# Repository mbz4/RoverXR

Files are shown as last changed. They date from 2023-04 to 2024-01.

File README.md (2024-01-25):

# RoverXR

OSHW EE000002

https://certification.oshwa.org/ee000002.html

## Open Source Teleop Demo For Students

Teleoperation { Low-Latency Video + Virtual Scene + M5 Rover C Pro} Fun

# Repository tree

```bash
📦RoverXR (edu_teleop_demo)
 ┣ 📂Blueprints
 ┃ ┣ 📂CAD
 ┃ ┣ 📂Figures
 ┃ ┣ 📂Firmware
 ┃ ┣ 📂Godot
 ┃ ┣ 📂Install
 ┃ ┣ 📂Testing
 ┃ ┣ 📜stream_mjpeg_ws.py
 ┃ ┗ 📜README.md
 ┣ 📂Thesisaurus
 ┃ ┣ 📂Future
 ┃ ┣ 📂Poster
 ┃ ┣ 📂Stream Testing
 ┃ ┣ 📂Survey
 ┃ ┣ 📂Workload Analysis
 ┃ ┣ 📜README.md
 ┃ ┗ 📜Zorec_XR_teleop_demo_dev_MSC.pdf
 ┣ 📜LICENSE
 ┗ 📜README.md
```

### BibTex

```
@misc{Zorec_2023, 
    title={XR TELEOPERATION DEMO DEVELOPMENT}, 
    url={https://github.com/mbz4/RoverXR}, 
    publisher={University of Tartu}, 
    author={Zorec, Matevž Borjan}, 
    year={2023}, 
    month={May},
    keywords = {teleoperation,godot-engine,video-streaming,augmented-reality,educational}
    }
```

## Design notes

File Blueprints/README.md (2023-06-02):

# Blueprints

## CAD, ELE, FW, HOW-TO

### Blueprints Tree

```
📦Blueprints
 ┣ 📂CAD
 ┣ 📂Figures
 ┣ 📂Firmware
 ┣ 📂Godot
 ┣ 📂Install
 ┣ 📂Testing
 ┣ 📜stream_mjpeg_ws.py
 ┗ 📜README.md
```

## Link to Pi2AR apk

[Pi2AR apk](https://drive.google.com/file/d/1Cv3eQTNefOODzdWp3nt191eAGhhzpHHq/view?usp=sharing)

## Link to 2D Demo scene

[2D demo executable](https://drive.google.com/file/d/1SQd6SBSPiZBGjC4s-J33E9EYQUEvNkwV/view?usp=sharing)

# Pi-Side Setup

0. flash Raspbian Lite (32-bit) onto SD Card (class 10 recommended), then run

    `sudo apt-get update && sudo apt-get upgrade -y`

    - expand filesystem, adjust settings, hostname, enable SSH etc
    
    `sudo raspi-config`
    
    - adjust network settings: Wifi, etc

1. get the repo to the pi

    `git clone https://github.com/mbz4/edu_teleop_demo.git`

2. to start streaming, running the following python script 

    `Blueprints/stream_mjpeg_ws.py`

    - it configures the camera using picamera2
    - prepares a byte buffer in memory
    - starts a websocket server at:

        `ws://<PI-IP>:3333`
    
    - once a client connects
        
        - it sends individual JPEG frames from picamera2 output buffer

# VR setup

1. get scene apk to your Meta Quest 2

    - once loaded you can use controller thumbsticks to rotate, navigate the AR scene
        - behind you is a terminal window
        - you can set the websocket URI address here - input just the Pi IP:

        `PI_IP > PI_IP_ADDRESS_IN_YOUR_LOCAL_NETWORK`

        - (make sure you are connected to the same network as the pi is)
    - disable space sense
    
2. run apk

# M5 Rover C setup

1. print mod kit file 

    - gcode (sliced for Prusa MK3S) found at:

    `Blueprints/CAD/32g_rover_mod_kit_0.3mm_PLA_MK3S_2h12m.gcode` 

    - v1 3mf model files found at:

    `Blueprints/CAD/rover_mod_kit.3mf`

2. assemble the mod kit
 
#### [Bill of materials for physical artefact](./CAD/README.md)

#### Fusion360 RoverXR assembly link [f360 assembly link](https://a360.co/4158f0r)

Please, note the above link may not function correctly if viewed on mobile.

#### v2 concept design for reference

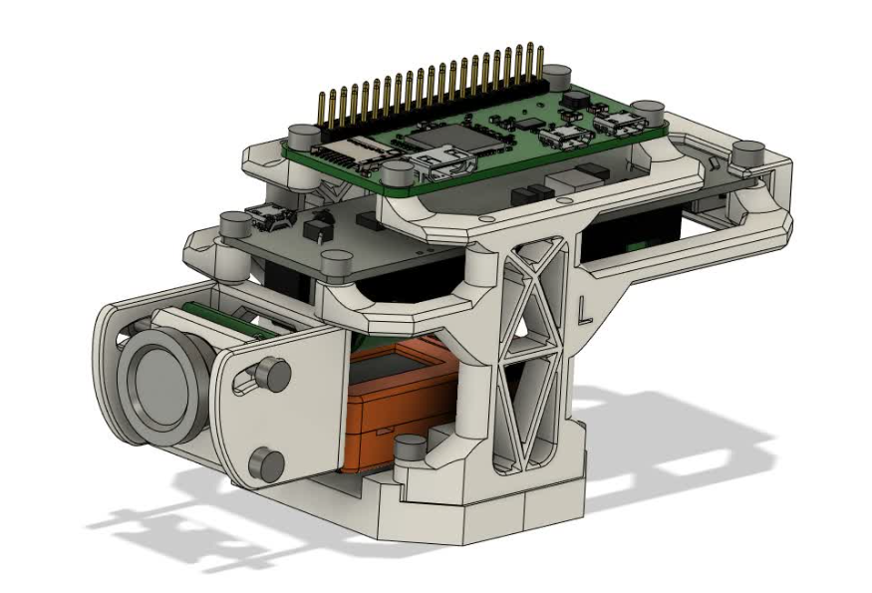
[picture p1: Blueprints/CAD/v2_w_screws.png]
Assembled v2 with screws


3. flash firmware, can use Arduino IDE (M5 Stick C library)

    - connect rover M5 Stick C to PC
    - open & flash master scripts, found at:

    `Blueprints/rover_FW/Master/Master.ino`

    - disconnect from PC and install Master Stick to Rover
    - connect remote M5 Stick C to PC
    - open & flash remote controller script, found at:

    `Blueprints/rover_FW/Remote/Remote.ino`

    - disconnect from PC and install Remote Stick to Remote Controller
    - use power switches on remote & rover
    - press and hold for 4 seconds the lower left side button on both M5 Stick C's to turn them on
    - press and hold for 4 seconds the 'M5' button on Remote controller, once the Master MAC address is shown
    - rover can now be remotely operated using remote

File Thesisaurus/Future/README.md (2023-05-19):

# Future Work Recommendations

graphic

|Title |Key points |Description |
|---|---|---|
|RoverXR  Hardware  Modifications|Integrate Pi Zero 2 W |Possible to bypass and omit M5 Stick C on the Rover and Remote. Zero 2 W could directly convey driving commands from VR  using a second websocket stream. The M5 Rovers battery can power the Zero 2 W directly. Improved multithreading enables more complex teleoperation solutions. |
| |New enclosed snap-fit shell|Design fully enclosed, transparent, compliant snap-fit shell for easy access  and a more seamless aesthetic.  Making it flexible and rounded should improve feel when handling. |
| |New camera |Install wide field of view camera with motorised focusing. |
| |Adjustable camera angle |Add servo for adjusting camera angle on the fly. Additionally, modify current camera mount to  accommodate additional 15 degrees to the downward facing angle. |
| |Add shutdown button |Expand breakout board with shutdown button for triggering poweroff command. |
| |Improve interface |Add more status indicators to better inform a user of status of the device  without having to SSH in.  This could include various assortment of LEDs or a small OLED. |
| |Develop a charging base |Currently the setup consists of two devices, easy to misplace. With a dedicated charging base/enclosure,  they would have a place to rest & recharge.  This would in turn help to reduce the risk of misplacement. |
| |Add sensors |Usually teleoperated robots are equipped with various sensors,  enabling extero- and proprioception. This could be used to complement  a new VR interface solution, which better informs the operator of both the status  of the vehicle as well as its surroundings. Three key sensory features to consider include: LiDAR, Microphone, battery voltage monitor. |
| |Remote controller mount |The current chassis could be extended by integrating  a simple remote controller mount. This may help reduce the chance of misplacing  either component as they are intended to work as a pair. |
|RoverXR Software Modifications  |Improve streaming solution |The video stream solution consists of two components: a RPi based server,  serving the video stream, and a Godot scene,  which connects to the server and displays the individual frames.  Investigating alternative protocols, encoding and rendering techniques  could improve the quality of the video stream. Remote streaming configuration should also be added, such as basic video quality settings etc. |
| |Godot |The overall scene can be expanded by adding more informative interfaces. |
| |Autonomous driving mode |With an upgraded RPi unit capable of controlling movement,  autonomous operation is easier to implement. |
| |Deploy ROS |This would allow for more complex teleoperation solutions, as well as provide topic based control and access to a wide variety of devices  with ready made drivers, making future development more cost effective. A Godot-ROS-Bridge could be implemented for a more seamless development experience. Ready made SLAM and autonomous driving solutions would also be available. However, this may require a further a more capable external compute component in the setup|
| |Control from VR |Implement RoverXR control interface in a Godot VR scene to control the movement. |
| |Godot H264 decoding |Explore ways for decoding video streams natively in Godot. One possible solution may be the 'ffmpeg-node' for Godot 3.x |
|RoverXR Evaluation Ideas |Unity solution |Prepare an equivalent interface using the Unity game engine to compare performance. |
| |Compare with FPV |Comparative study to commercial drone FPV setups,  like the DJI FPV Combo product series. An OpenHD and EZ-WiFiBroadcaster implementation should also be explored.  These represent some of the most comprehensive and best performing FPV solutions. |
| |Further evaluate solution  |Ideas to explore, such as evaluating interface intuitiveness/immersiveness,  setup complexity, task completion time etc |

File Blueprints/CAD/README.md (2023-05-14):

# CAD Tree

```
📦CAD
 ┣ 📂v1
 ┃ ┣ 📜32g_rover_mod_kit_0.3mm_PLA_MK3S_2h12m.gcode
 ┃ ┣ 📜rover_mod_kit.3mf
 ┃ ┗ 📜v1.png
 ┣ 📂v2
 ┃ ┣ 📂3mf
 ┃ ┃ ┣ 📂deprecated
 ┃ ┃ ┃ ┣ 📜assorted_camera_mounts.3mf
 ┃ ┃ ┃ ┣ 📜camera_mounting_shroud v15.3mf
 ┃ ┃ ┃ ┣ 📜camera_mounting_shroud v16.3mf
 ┃ ┃ ┃ ┣ 📜camera_mounting_shroud_3,04mm_focal_adjust v10.3mf
 ┃ ┃ ┃ ┣ 📜camera_mounting_shroud_3,04mm_focal_adjust v11.3mf
 ┃ ┃ ┃ ┗ 📜rear_port_bumber v32.3mf
 ┃ ┃ ┣ 📜adjustable_camera_shroud_mount_w_lens.3mf
 ┃ ┃ ┣ 📜bumper_maglock_adapter v23.3mf
 ┃ ┃ ┣ 📜bumper_maglock_adapter_cap v23.3mf
 ┃ ┃ ┣ 📜camera_mounting_shroud v21.3mf
 ┃ ┃ ┣ 📜joy_c_remote_adapter v22.3mf
 ┃ ┃ ┣ 📜joy_c_remote_adapter_cap v22.3mf
 ┃ ┃ ┣ 📜maglock_adapter_kit.3mf
 ┃ ┃ ┣ 📜mounting_adapter_v2 v66.3mf
 ┃ ┃ ┗ 📜rear_port_bumber v34.3mf
 ┃ ┣ 📂f3z
 ┃ ┃ ┗ 📜assembly v68.f3z
 ┃ ┣ 📂step
 ┃ ┃ ┣ 📜adjustable_camera_shroud_mount_w_lens.step
 ┃ ┃ ┣ 📜assembly v68.step
 ┃ ┃ ┣ 📜camera_mounting_shroud.step
 ┃ ┃ ┣ 📜mounting_adapter_v2 v66.step
 ┃ ┃ ┗ 📜rear_port_bumber v32.step
 ┃ ┣ 📜38g_full_mod_kit_v2_0.2mm_PLA_MK3S_4h47m.gcode
 ┃ ┣ 📜3g_maglock_adapter_kit_0.2mm_PLA_MK3S_29m.gcode
 ┃ ┣ 📜mod_kit_v2.3mf
 ┃ ┣ 📜v2.png
 ┃ ┗ 📜v2_w_screws.png
 ┣ 📜assembly v77.avi
 ┣ 📜README.md
 ┣ 📜v0_concept_phase.png
 ┣ 📜v1.png
 ┗ 📜v2_w_screws.png
```

# Bill of materials

|Component |Description |Features |QTY|Cost Per  [EUR]|Cost  [EUR]|
|---|---|---|---|---|---|
|M5 Rover C Pro |Programmable Mecanum wheel omnidirectional robot base. 4x N20 worm gear motors to drive the wheels directly by the motor driver. Servo gripping mechanism. |I2C Address 0x38, remote control, gripper Programmable, Four-channel motor driver, Extra Grove ports for expansion, STM32F030C6T6, I2C 16340(700mAh) battery holder|1  |60 |60 |
|Wemos Battery Shield |18650 Battery Shield (V3) for Raspberry Pi & Arduino Cheap, portable power supply module. |In: 5V/500mA (Micro USB) Out: 5VDC (USB type A) 3x 5VDC (up to 4A) + 3x 3VDC (up to 1A) Battery Charging /  Charged LEDs Overcharge, Deep Discharge Protection |1  |2.5 |2.5 |
|18650 Li-Ion |Battery: Samsung Li-Ion 18650 cell |3.6V 2600mAh |1  |11 |11 |
|M5StickC ESP32 |M5 Stick C is a mini M5 Stack, powered by ESP32.  It is a portable, easy-to-use, open source, IoT development board. |ESP32-based, IMU, LED, IR, Mic,  3 buttons, LCD(0.96 in), battery Wearable / Wall mounted, support: UIFlow, MicroPython, Arduino, .NET nanoFramework |2  |13.7 |27.4 |
|JoyC Omni-directional Controller|Rocker module for the M5 Stick C & Rover base. |STM32F030F4, I2C, 12 RGB LEDs omni-directional movement & button press  16340 battery holder |1  |18.2 |18.2 |
|Raspberry Pi Zero 1 W v1.3 |Flexible, compact Raspberry Pi Single Board Computer. Size: 65mm long by 30mm wide, affordable. |1GHz single-core CPU, 512MB RAM Mini HDMI port, Micro USB OTG port Micro USB power, HAT-compatible 40-pin header CSI camera connector WiFi (2.4GHz) & Bluetooth |1  |13.7 |13.7 |
|Raspberry Pi Camera Board v2.1  |High quality camera based on Sony IMX219PQ image sensor. Supports FHD video and still photographs. |Fixed focus lens, 8 megapixel resolution  Support 1080p30, 720p60, 480p90 25mm x 23mm x 9mm, just over 3g; CSI connector |1  |23.65 |23.65 |
|CSI Camera Ribbon Adapter |Raspberry Pi Zero adapter cable to Camera CSI connector |Length: 15 cm, CSI 22-pin (Pi Zero) to 15-pin (Camera board) |1  |5.12 |5.12 |
|0.67x Wide Angle, Macro, Fisheye|Magnetic interlocking lens camera add-on kit |Self-adhesive metal ring mount 0.67x wide angle, macro lens combo 180 deg field of view fisheye lens |1  |7 |7 |
|Totals |Listed Prices: April 2023 |Total Part Count: |10 |Total [EUR]: |168.57 |

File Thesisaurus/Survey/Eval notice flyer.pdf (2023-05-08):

### Ad hoc event notice:

## Thesis artefact evaluation

## From 15:00 Until 18:00

## Please, do not interrupt ongoing experiments

If you wish to partake or have concerns, please contact student responsible.

If you’d like to help me evaluate and experience a cool new teleop demo, please talk to me for a testing slot!

Student responsible: Matevž Zorec Contact: matevz.zorec@gmail.com

Tartu, May 9

th 2023

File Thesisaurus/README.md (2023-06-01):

# Thesisaurus Tree

## Defense presentation link

[XR TELEOP DEMO DEV](https://docs.google.com/presentation/d/17Uub06jR5xMtjwQKw79iaS7XjQxCx0AH1VZ0uDm-VvA/edit?usp=sharing)

```
 ┣ 📂Future
 ┃ ┗ 📜README.md
 ┣ 📂Poster
 ┃ ┗ 📜A0_mbz_XR_Demo_poster.pdf
 ┣ 📂Stream Testing
 ┃ ┗ 📜README.md
 ┣ 📂Survey
 ┃ ┣ 📂evaluation_event
 ┃ ┃ ┣ 📜20230509_155246.mp4
 ┃ ┃ ┣ 📜20230509_160718.mp4
 ┃ ┃ ┗ 📜blurred_out_survey_participant.jpg
 ┃ ┣ 📂word_clouds
 ┃ ┃ ┣ 📜how_do_you_feel_about_the_interface_in_the_setup.png
 ┃ ┃ ┣ 📜please_describe_the_rover.png
 ┃ ┃ ┣ 📜please_describe_your_experience_with_the_rover.png
 ┃ ┃ ┣ 📜please_share_your_thoughts_on_how_to_improve_the_setup.png
 ┃ ┃ ┣ 📜ROSETTA_how_do_you_feel_about_the_interface_in_the_setup.png
 ┃ ┃ ┣ 📜ROSETTA_please_describe_the_rover.png
 ┃ ┃ ┣ 📜ROSETTA_please_describe_your_experience_with_the_rover.png
 ┃ ┃ ┗ 📜ROSETTA_please__share_your_thoughts_on_how_to_improve_the_overall_setup.png
 ┃ ┣ 📜Eval notice flyer.pdf
 ┃ ┗ 📜README.md
 ┣ 📂Workload Analysis
 ┃ ┗ 📜README.md
 ┗ 📜README.md
```

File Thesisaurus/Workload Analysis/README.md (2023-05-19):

# Extended Thesis Workload Analysis

|Task |Description |Time  Invested  [hrs]|
|---|---|---|
|VR & background |- read:  “The VR Book: Human-Centered Design for Virtual Reality” by Jason Jerald - preliminary literature review - understanding teleoperation, motivation - isolating problem statement |25 |
|Reviewing previous works |- reviewing previous teleoperation thesis works - experience teleoperating & developing with Donkey Car S1 - studying artefact implementations in previous works - formulating preliminary objectives |15 |
|Network communication 101 |- reviewing network communication protocols - WebRTC, WebSockets, UDP, RTSP, TCP - studying associated documentation - collecting example implementations on github - testing basic UDP, TCP, WebSocket communication with Python |20 |
|Video streaming, encoding 101 |- learning about how video streaming works - exploring picamera & picamera2 library implementation - exploring, collecting ESP32-CAM streaming solutions - learning about video encoding & codecs - learning about video streaming |20 |
|Testing video streaming |- testing DietPi Motion Eye video streaming w/ RPi 3B+ - testing ESP32-CAM video streaming - testing DroidCam & DroidCam OBS plugin - testing raspivid video streaming using TCP and using UDP - testing picamera & picamera2/libcamera video capture - collecting documentation - assessing viability - learning with MPV video player - experimenting with MPV video player - measuring latency using Droste effect & stopwatch |45 |
|Reviewing Meta Quest 2 |- reviewing specificatons - learning about VR HMDs - getting familiar with the virtual environment - setting up development environment |20 |
|Investigating M5 products |- understanding M5 products & value - studying Rover C Pro & Joy C Remote implementation - collecting documentation, various example projects - exploring library examples - studying rover UDP control communication solution - exploring UI Flow & M5 Burner utilities - testing various example rover & remote configurations - developing servo control feature |20 |
|Exploring Godot Engine |- getting familiar with Godot Engine v3 & v4 - watching various tutorials - trying various demonstration projects - developing own learning/test projects - exploring documentation - testing, exploring example solutions - understanding development flow - getting familiar with interface - exploring GDScript - learning about OpenXR, WebXR, Godot-xr-tools - troubleshooting development issues - learning about Android development, incl. Gradle & ADB - communicating on Godot Engine official discord server - preparing demo communication projects - developing VR scene - developing AR scene - developing final frictionless scene|65 |
|Designing RoverXR |- layout, design brainstorming - component selection & testing - extracting key design requirements - development environment setup - collecting 3D models - preparing reference base model - validating reference base model - designing initial solution - iterating initial solution - test print & validating - printing, assembling, testing v1 - breakout board development - isolating improvement focus areas - iterating v1 towards v2, adding/improving features - printing, assembling, testing v2 |85 |
|Developing RPi Streaming |- preparing Raspberry Pi Zero 1 W - testing power consumption - configuring development environment - testing compute capabilities - developing streaming solution |30 |
|Evaluating artefact |- planning evaluation - assembling evaluation checklist - outlining evaluation objectives - preparing survey - collecting, assembling data - analyzing results |25 |
|Thesis writeup |- planning writeup - collecting materials, notes etc - writeup & iterations |95 |
|Total tasks completed  Total time invested|12 |465 |

graphic

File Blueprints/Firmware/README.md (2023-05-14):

# Firmware tree

```
📦Firmware
 ┣ 📂M5_RoverC-0.0.1-Library
 ┃ ┣ 📂examples
 ┃ ┃ ┣ 📂RoverC_M5StickC
 ┃ ┃ ┃ ┣ 📂JoyC_&_RoverC
 ┃ ┃ ┃ ┃ ┣ 📂Master
 ┃ ┃ ┃ ┃ ┃ ┗ 📜Master.ino
 ┃ ┃ ┃ ┃ ┗ 📂Remote
 ┃ ┃ ┃ ┃ ┃ ┣ 📜icon.c
 ┃ ┃ ┃ ┃ ┃ ┗ 📜Remote.ino
 ┃ ┃ ┃ ┗ 📂RunningRoverC
 ┃ ┃ ┃ ┃ ┗ 📜RunningRoverC.ino
 ┃ ┃ ┣ 📂RoverC_M5StickCPlus
 ┃ ┃ ┃ ┣ 📂JoyC_&_RoverC
 ┃ ┃ ┃ ┃ ┣ 📂Master
 ┃ ┃ ┃ ┃ ┃ ┗ 📜Master.ino
 ┃ ┃ ┃ ┃ ┗ 📂Remote
 ┃ ┃ ┃ ┃ ┃ ┣ 📜icon.c
 ┃ ┃ ┃ ┃ ┃ ┗ 📜Remote.ino
 ┃ ┃ ┃ ┗ 📂RunningRoverC
 ┃ ┃ ┃ ┃ ┗ 📜RunningRoverC.ino
 ┃ ┃ ┗ 📂RunningRoverC
 ┃ ┃ ┃ ┗ 📜RunningRoverC.ino
 ┃ ┣ 📂src
 ┃ ┃ ┣ 📜M5_RoverC.cpp
 ┃ ┃ ┗ 📜M5_RoverC.h
 ┃ ┣ 📜library.json
 ┃ ┣ 📜library.properties
 ┃ ┣ 📜LICENSE
 ┃ ┗ 📜README.md
 ┣ 📂Remote
 ┃ ┣ 📜icon.c
 ┃ ┗ 📜Remote.ino
 ┣ 📂Rover
 ┃ ┗ 📜Rover.ino
 ┗ 📜README.md
 ```

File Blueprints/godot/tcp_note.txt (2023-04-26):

1. declaring variables:
can use var variable_name: variable type
var tcp_connection: StreamPeerTCP = StreamPeerTCP.new()

2. leave the _ready function alone

3. how to add a signal definition (at the top of the script):
signal signal_name(variables, to, pass, ...)

4. use _process func (per frame exec: equivalent to polling perhaps)
invoking tcp_conn.get_available_bytes()
... if > 0 ==> invoke get_data...
... if data > 0...
🙂
else:
😦

5. if tcp_conn is lost
set process false 

6. match statement is a thing

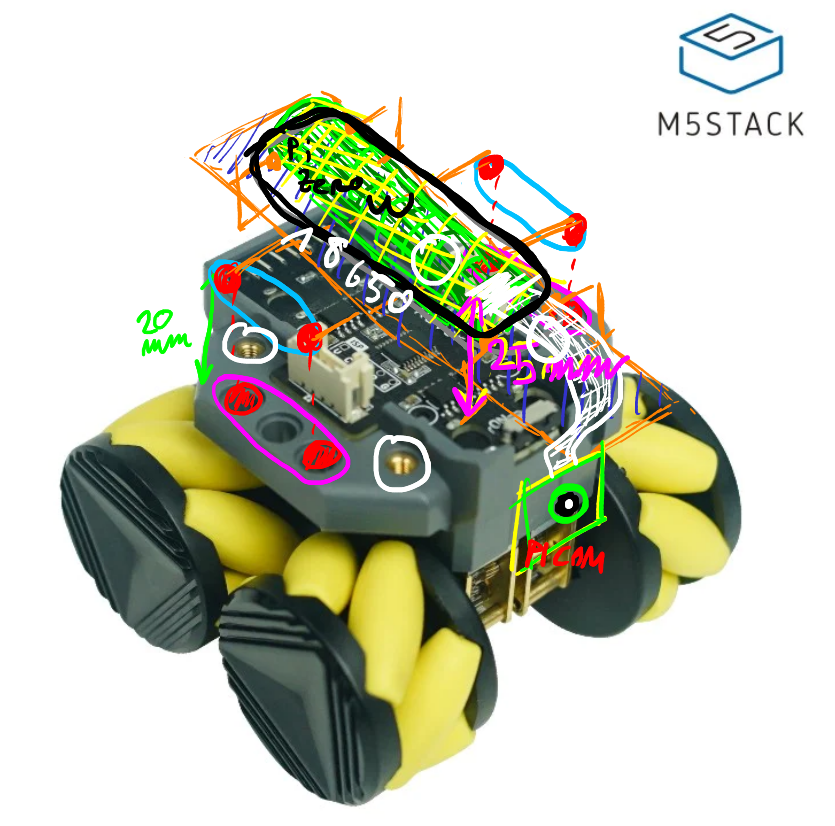
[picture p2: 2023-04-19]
Blueprints/Figures/M5Rover/v0_concept_phase.png

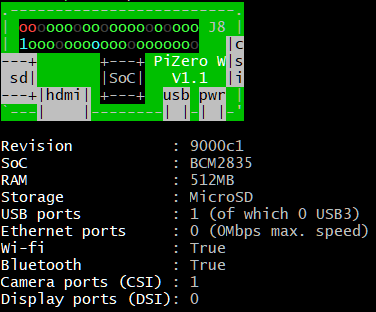
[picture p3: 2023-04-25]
Blueprints/Figures/RPi/pi_zero_pinout.png

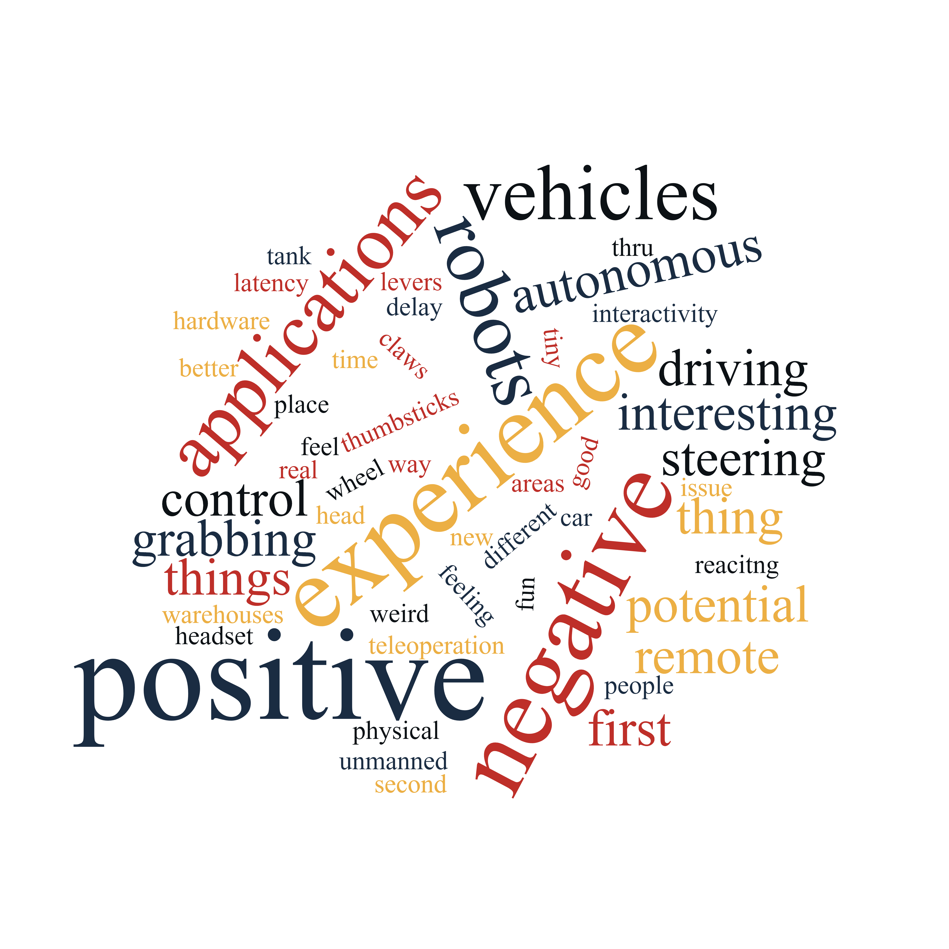
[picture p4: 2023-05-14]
Thesisaurus/Survey/word_clouds/ROSETTA_please_describe_your_experience_with_the_rover.png

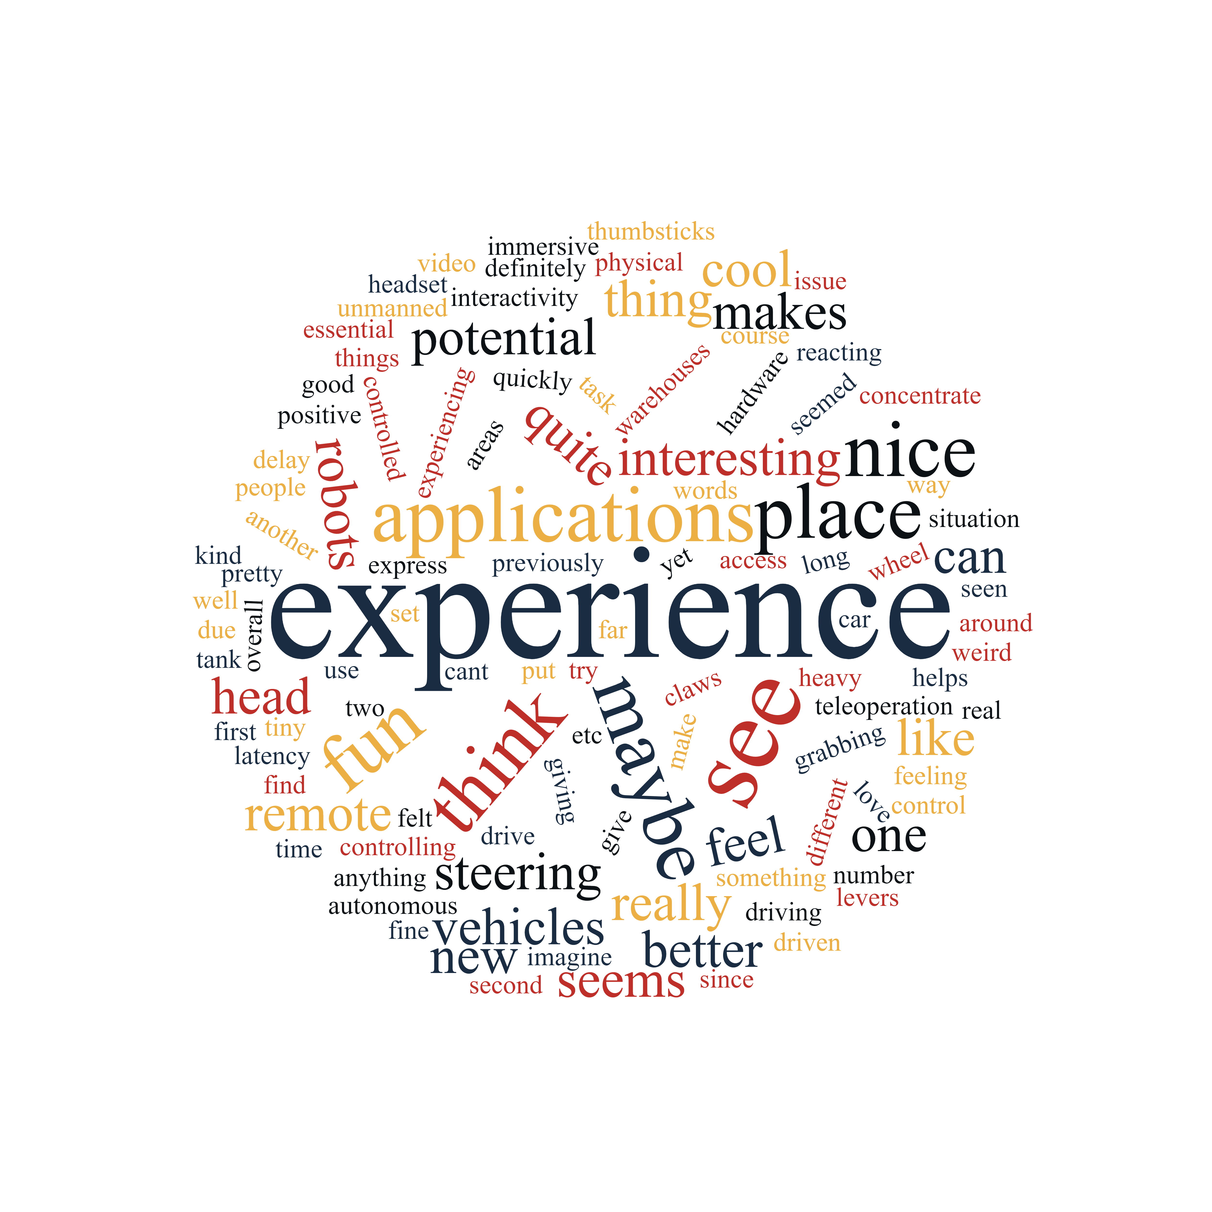
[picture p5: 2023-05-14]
Thesisaurus/Survey/word_clouds/please_describe_your_experience_with_the_rover.png

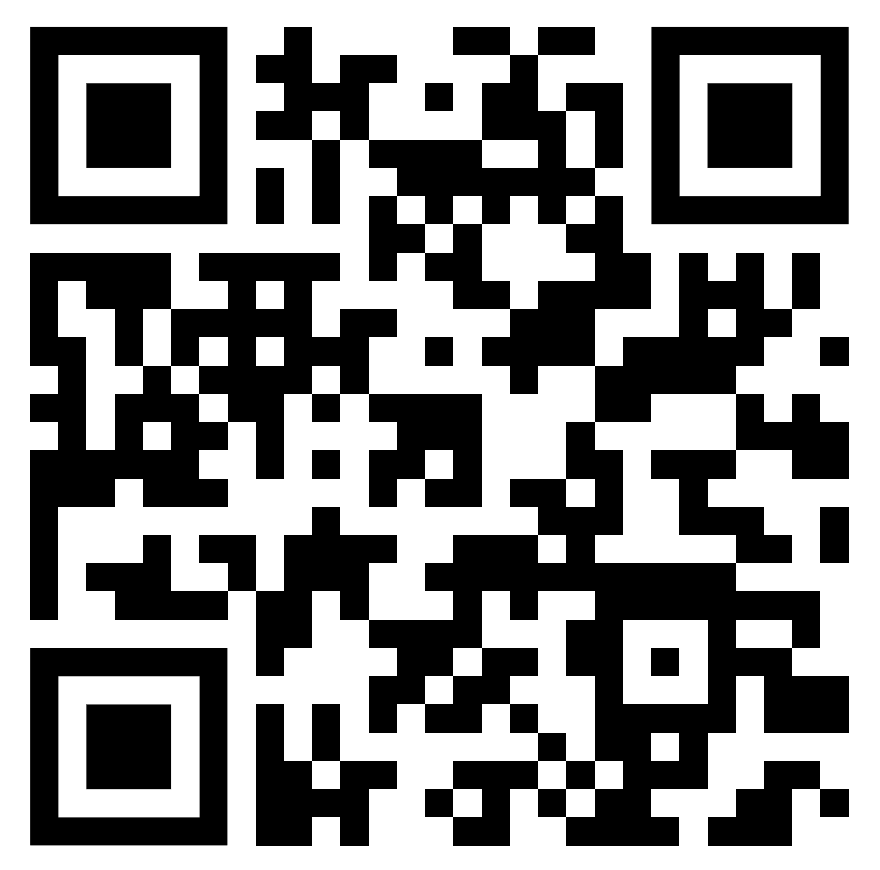
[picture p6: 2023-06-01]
Thesisaurus/roverXR_QR.png

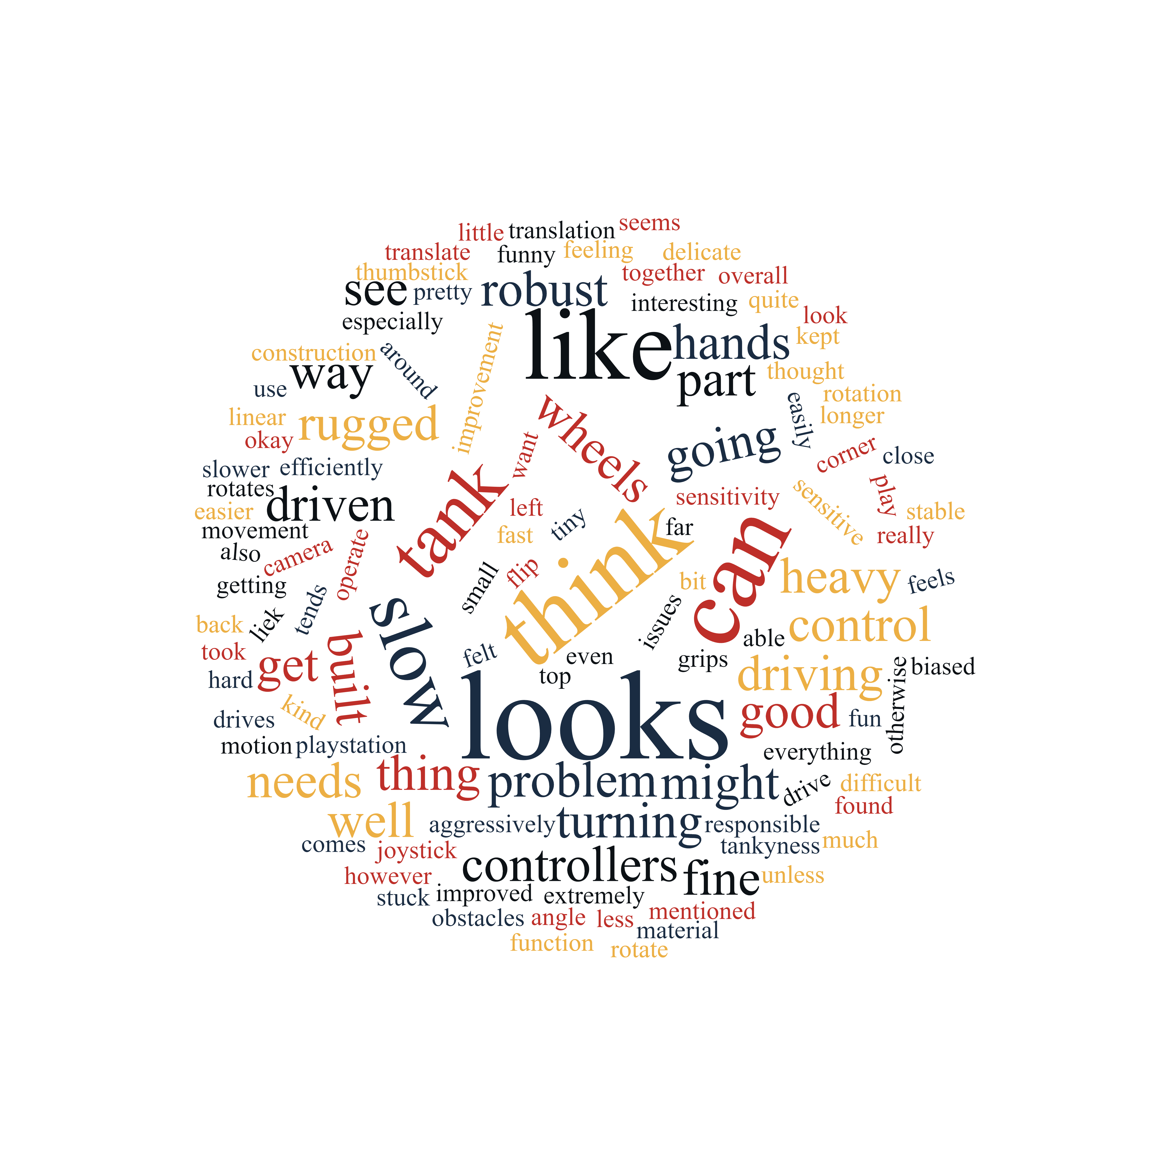
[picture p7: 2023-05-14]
Thesisaurus/Survey/word_clouds/please_describe_the_rover.png

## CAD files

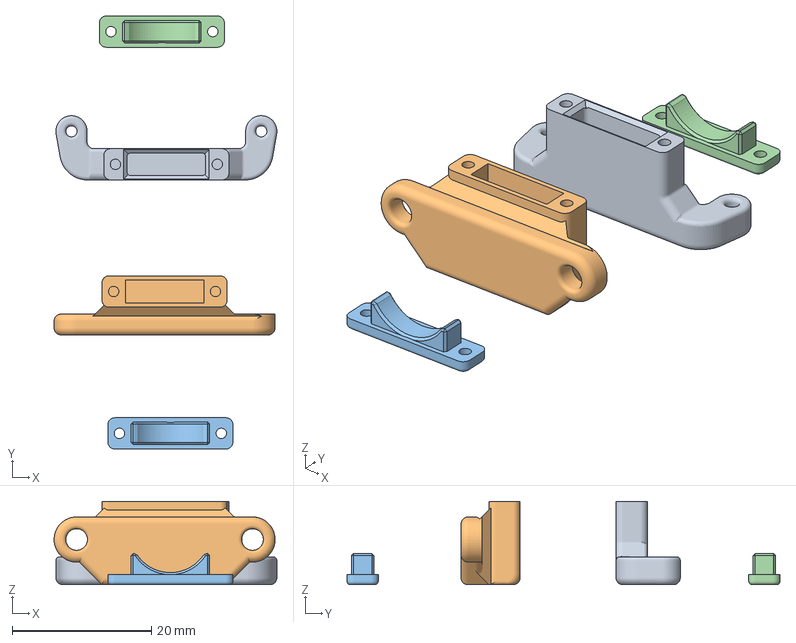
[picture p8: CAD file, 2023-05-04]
Blueprints/CAD/v2/3mf/maglock_adapter_kit.3mf
32.0 x 62.3 x 12.0 mm
joy_c_remote_adapter v22
bumper_maglock_adapter v23
bumper_maglock_adapter_cap v23
joy_c_remote_adapter_cap v22

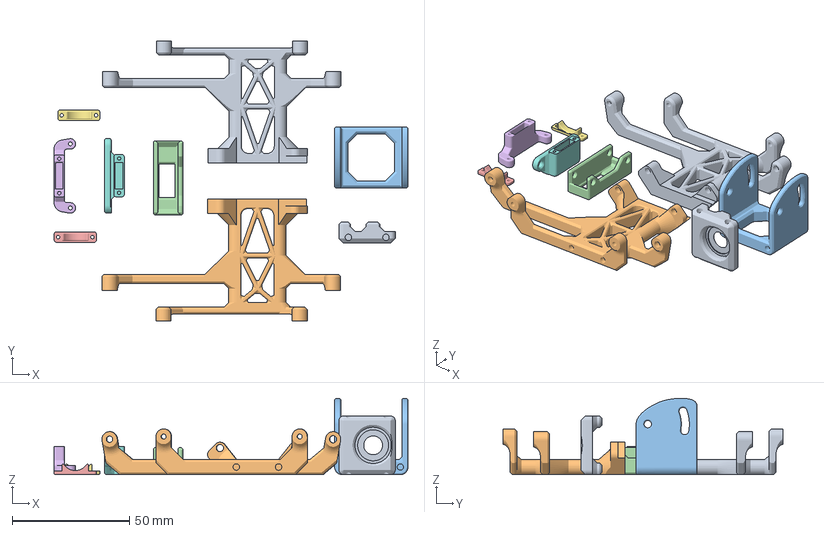
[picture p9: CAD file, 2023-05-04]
Blueprints/CAD/v2/mod_kit_v2.3mf
150.9 x 119.5 x 32.5 mm
L
R
adjustable_camera_shroud_mount_w_lens
rear_port_bumber v34
joy_c_remote_adapter_cap v22
joy_c_remote_adapter v22
bumper_maglock_adapter_cap v23
bumper_maglock_adapter v23
camera_mounting_shroud v21

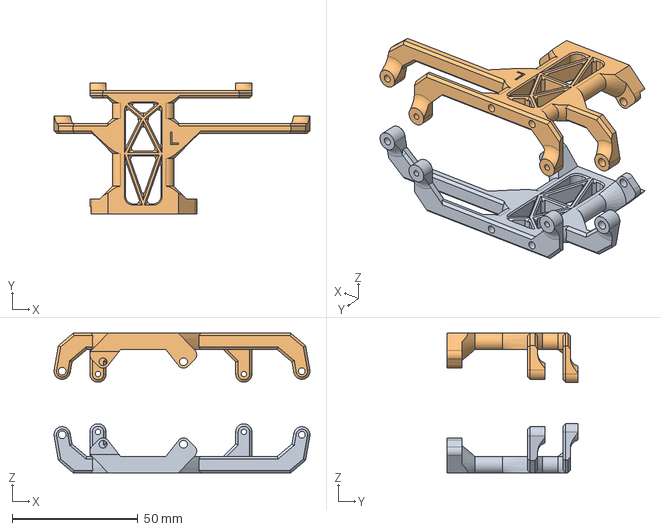
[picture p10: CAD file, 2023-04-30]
Blueprints/CAD/v2/step/mounting_adapter_v2 v66.step
101.8 x 52.0 x 55.5 mm

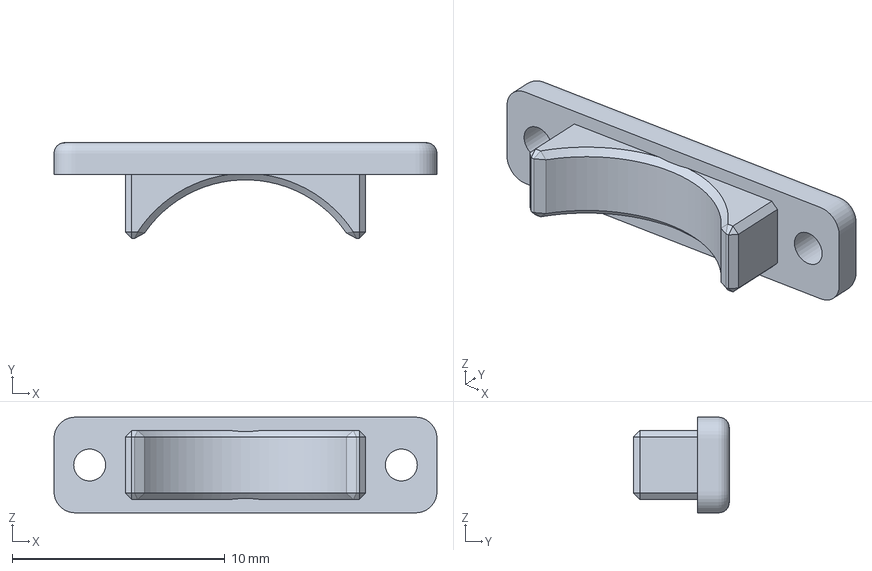
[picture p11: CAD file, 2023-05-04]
Blueprints/CAD/v2/3mf/bumper_maglock_adapter_cap v23.3mf
18.0 x 4.50 x 4.50 mm

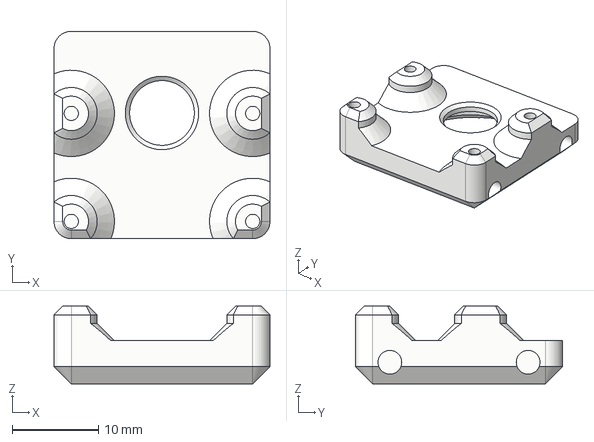
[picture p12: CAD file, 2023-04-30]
Blueprints/CAD/v2/step/camera_mounting_shroud.step
25.0 x 24.0 x 9.00 mm

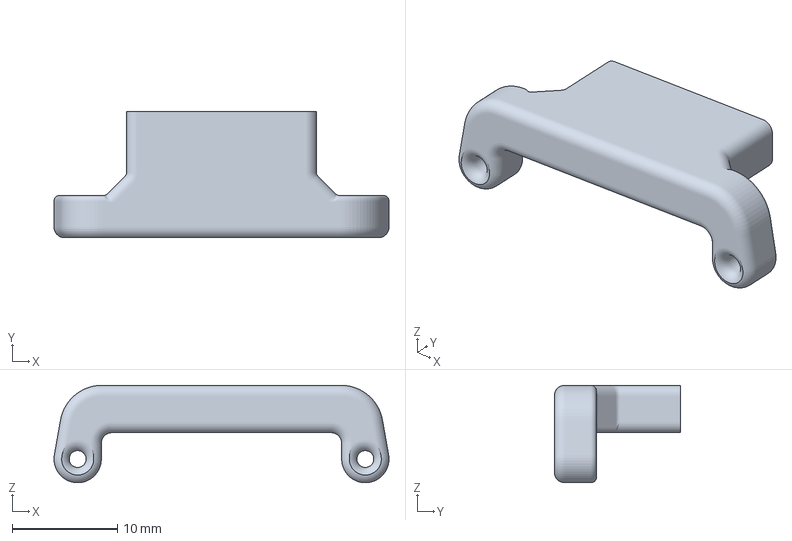
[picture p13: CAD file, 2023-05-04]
Blueprints/CAD/v2/3mf/joy_c_remote_adapter v22.3mf
31.8 x 12.0 x 9.25 mm

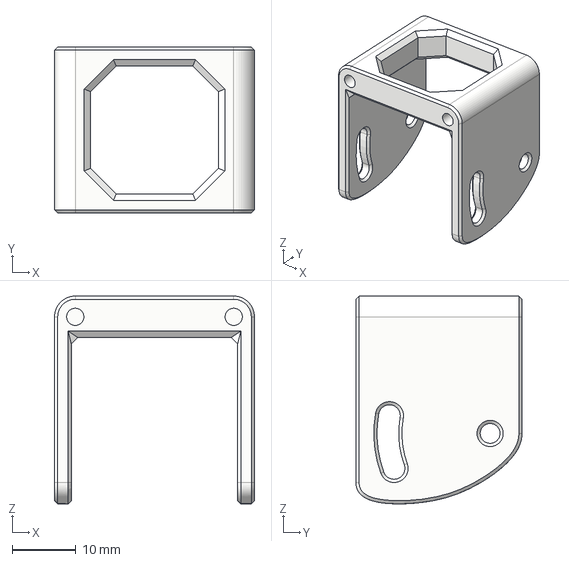
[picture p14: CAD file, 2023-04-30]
Blueprints/CAD/v2/step/adjustable_camera_shroud_mount_w_lens.step
31.3 x 26.0 x 32.5 mm

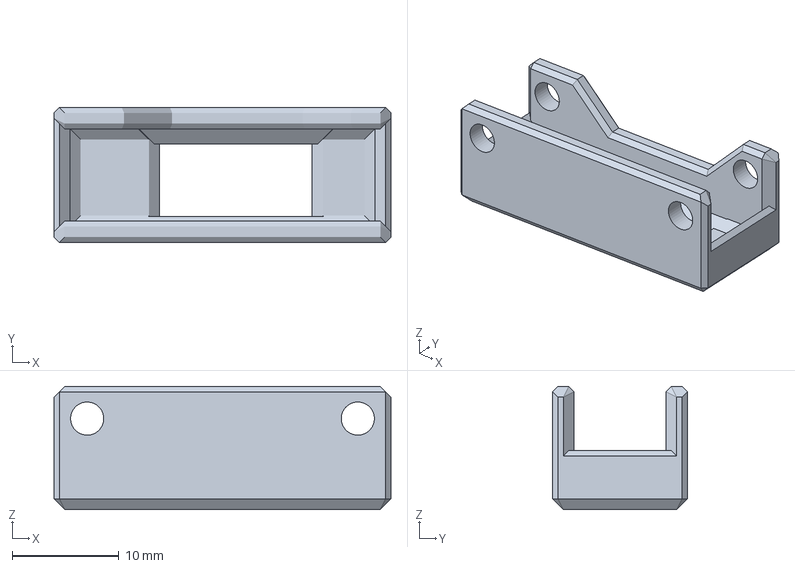
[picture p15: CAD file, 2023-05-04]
Blueprints/CAD/v2/3mf/rear_port_bumber v34.3mf
31.5 x 12.6 x 11.5 mm

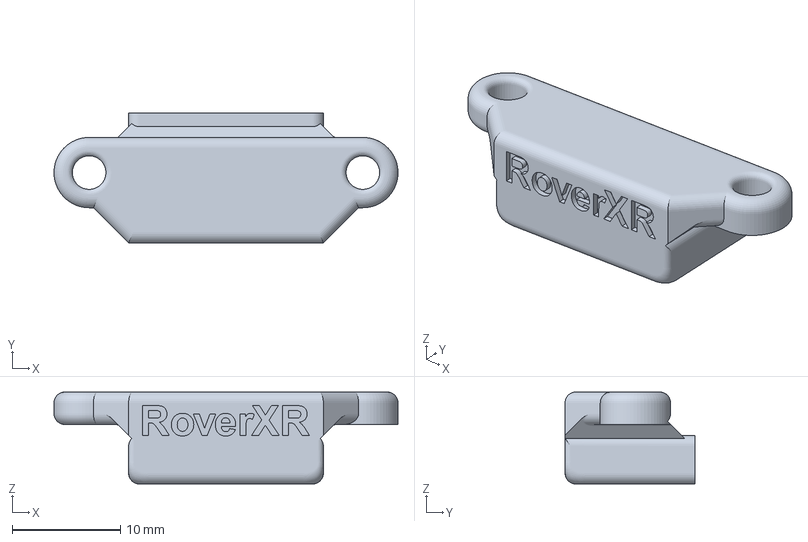
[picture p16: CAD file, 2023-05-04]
Blueprints/CAD/v2/3mf/bumper_maglock_adapter v23.3mf
31.8 x 12.0 x 8.50 mm

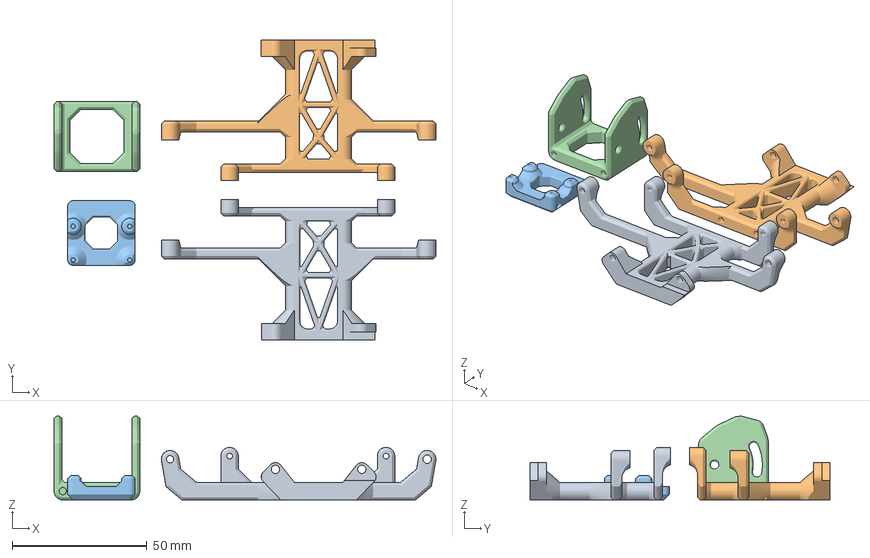
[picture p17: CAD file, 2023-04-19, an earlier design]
Blueprints/CAD/v1/rover_mod_kit.3mf
141.6 x 111.1 x 31.1 mm
L
R
camera_mounting_plate
adjustable_camera_mount

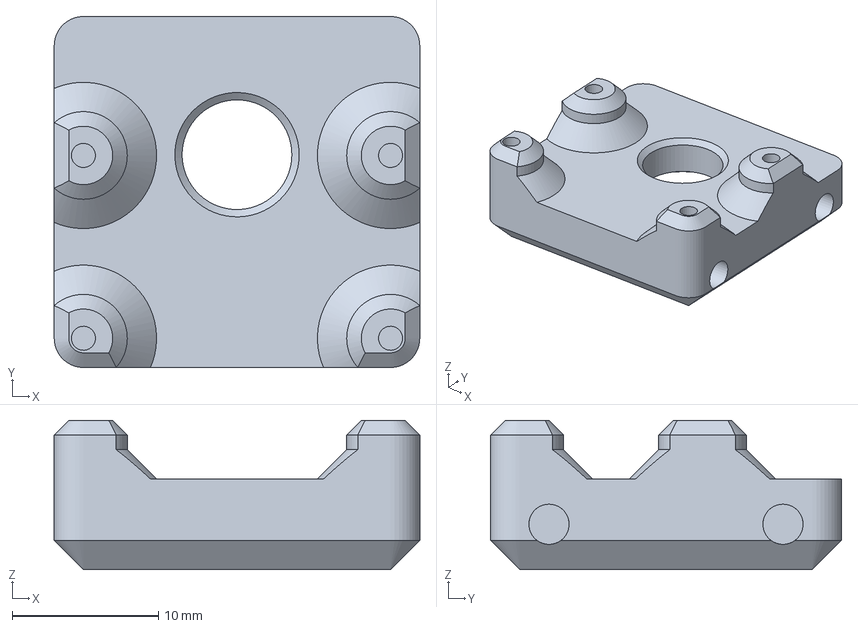
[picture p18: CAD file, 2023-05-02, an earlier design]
Blueprints/CAD/v2/3mf/deprecated/camera_mounting_shroud_3,04mm_focal_adjust v11.3mf
25.0 x 24.0 x 10.2 mm

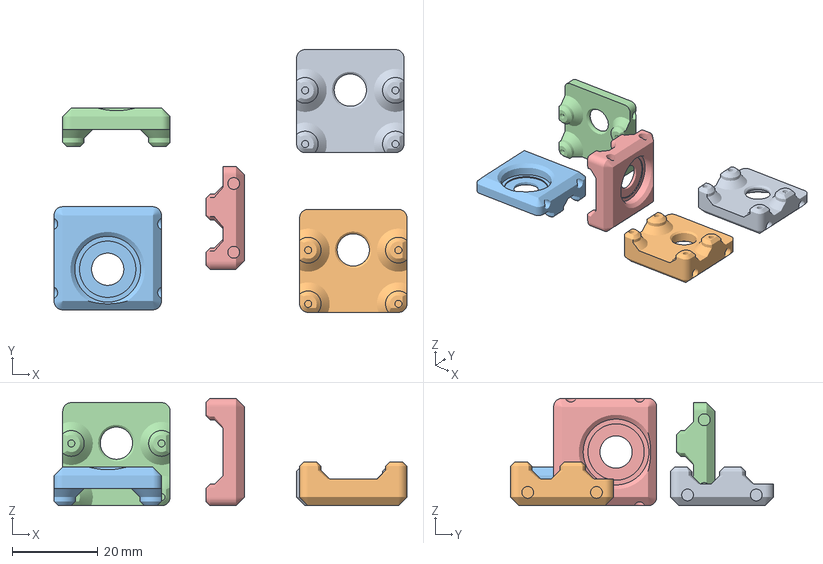
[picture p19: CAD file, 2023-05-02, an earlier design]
Blueprints/CAD/v2/3mf/deprecated/assorted_camera_mounts.3mf
82.2 x 61.2 x 25.0 mm
camera_mounting_shroud v16
camera_mounting_shroud_3,04mm_focal_adjust v11
camera_mounting_shroud v15 x 3

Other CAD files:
Blueprints/CAD/v2/step/rear_port_bumber v32.step
Blueprints/CAD/v2/3mf/joy_c_remote_adapter_cap v22.3mf
Blueprints/CAD/v2/3mf/camera_mounting_shroud v21.3mf
Blueprints/CAD/v2/3mf/deprecated/rear_port_bumber v32.3mf
Blueprints/CAD/v2/3mf/deprecated/camera_mounting_shroud v16.3mf
Blueprints/CAD/v2/3mf/deprecated/camera_mounting_shroud_3,04mm_focal_adjust v10.3mf
Blueprints/CAD/v2/3mf/adjustable_camera_shroud_mount_w_lens.3mf
Blueprints/CAD/v2/3mf/deprecated/camera_mounting_shroud v15.3mf
Blueprints/CAD/v2/3mf/mounting_adapter_v2 v66.3mf

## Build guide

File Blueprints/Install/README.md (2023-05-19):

# Autostart service installation scripts

### To set up streaming on boot, run in terminal on the RPi (in this directory):

```bash
./install.sh
``` 

* for reference a correctly configured RoverXR takes up to ~5' from boot to stream

* please note websockets is required, to install use:

```bash
pip install websockets
```

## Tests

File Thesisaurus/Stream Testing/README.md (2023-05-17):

# Stream Testing

## Delay vs App, Protocol, Router

Stream delay vs Application, Protocol, Router

## Detailed Stream Testing Information

|Tested date |Application |Arguments |Network Router |Frequency  Range|Measured  px2px  delay [ms]|Device source |Source platform |Device sink |Sink platform |Sink application |Sink application arguments |Source sensor |Stream Resolution|Encoding|Protocol |Git source |Git sink |Comments |
|---|---|---|---|---|---|---|---|---|---|---|---|---|---|---|---|---|---|---|
|15. 03. 2023|DroidCam OBS |tcp IP (set in OBS) |[GL-SF1200 Dual-band gigabit Router](https://www.gl-inet.com/products/gl-sf1200/) |5GHz |160 |[Samsung Galaxy Note10](https://www.gsmarena.com/samsung_galaxy_note10-9788.php) |Android 12 |[OMEN Laptop 15-en1013dx Product Specifications](https://support.hp.com/ee-en/document/c07073462#AbT0)|64-bit Ubuntu 20.04 LTS|OBS 29.0.2 |MJPEG, use WiFi IP, Enable audio, Allow hardware acceleration, deactivate when not showing |[Samsung 12M Ultrawide AF Camera Module](https://www.samsungsem.com/global/product/module/camera-module.do)|1920x1080 |MJPEG |TCP |[droidcam-obs-git](https://github.com/dev47apps/droidcam-obs-plugin) |[obs-studio-git](https://github.com/obsproject/obs-studio) |butter smooth, crystal clear, fast |
|15. 03. 2023|raspivid |raspivid -fps 30 -t 0 -l -w 1920 -h 1080 -o udp://0.0.0.0:3333 |[GL-SF1200 Dual-band gigabit Router](https://www.gl-inet.com/products/gl-sf1200/) |2.4GHz |260 |[Raspberry Pi 4 Model B](https://www.raspberrypi.com/products/raspberry-pi-4-model-b/) |Raspberry Pi OS (64-bit) Lite|[OMEN Laptop 15-en1013dx Product Specifications](https://support.hp.com/ee-en/document/c07073462#AbT0)|64-bit Ubuntu 20.04 LTS|mpv_0.35.1+fruit.2_amd64.deb 2023-01-30 |mpv --hwdec=auto --cache=no --no-correct-pts --fps=30 --profile=low-latency --opengl-glfinish=yes udp://0.0.0.0:3333|Sony IMX219 |1920x1080 |H264 |UDP |[raspivid-git](https://github.com/raspberrypi/userland/blob/master/host_applications/linux/apps/raspicam/RaspiVid.c)|[mpv-player-git](https://github.com/mpv-player/mpv) |stable, lossy when shaken |
|15. 03. 2023|raspivid |raspivid -fps 30 -t 0 -l -w 1920 -h 1080 -o tcp://0.0.0.0:3333 |[GL-SF1200 Dual-band gigabit Router](https://www.gl-inet.com/products/gl-sf1200/) |2.4GHz |260 |[Raspberry Pi Zero W](https://www.raspberrypi.com/products/raspberry-pi-zero-w/) |Raspberry Pi OS (32-bit) Lite|[OMEN Laptop 15-en1013dx Product Specifications](https://support.hp.com/ee-en/document/c07073462#AbT0)|64-bit Ubuntu 20.04 LTS|mpv_0.35.1+fruit.2_amd64.deb 2023-01-30 |mpv --cache=no --no-correct-pts --fps=30 --profile=low-latency tcp://192.168.8.163:3333 |Sony IMX219 |1920x1080 |H264 |TCP |[raspivid-git](https://github.com/raspberrypi/userland/blob/master/host_applications/linux/apps/raspicam/RaspiVid.c)|[mpv-player-git](https://github.com/mpv-player/mpv) |smooth, stable |
|16. 03. 2023|raspivid |raspivid -fps 30 -t 0 -l -w 1920 -h 1080 -o tcp://0.0.0.0:3333 |[TL-WR802N 300Mbps N Nano Router](https://www.tp-link.com/us/home-networking/wifi-router/tl-wr802n/#specifications)|2.4GHz |380 |[Raspberry Pi 3 Model B+](https://www.raspberrypi.com/products/raspberry-pi-3-model-b-plus/)|Raspberry Pi OS (64-bit) Lite|[Samsung Galaxy Note10](https://www.gsmarena.com/samsung_galaxy_note10-9788.php) |Android 12 |mpv-android 2023-02-27-release |mpv --cache=no --no-correct-pts --fps=30 --profile=low-latency tcp://<source device LAN IP>:3333 |Sony IMX219 |1920x1080 |H264 |TCP |[raspivid-git](https://github.com/raspberrypi/userland/blob/master/host_applications/linux/apps/raspicam/RaspiVid.c)|[mpv-android-git](https://github.com/mpv-android/mpv-android) |slightly jittery, borderline unstable  [pi-camera#hardware-specification](https://www.raspberrypi.com/documentation/accessories/camera.html#hardware-specification)|
|17. 03. 2023|DroidCam OBS |tcp IP (set in OBS) |[TL-WR802N 300Mbps N Nano Router](https://www.tp-link.com/us/home-networking/wifi-router/tl-wr802n/#specifications)|2.4GHz |200 |[Samsung Galaxy Note10](https://www.gsmarena.com/samsung_galaxy_note10-9788.php) |Android 12 |[OMEN Laptop 15-en1013dx Product Specifications](https://support.hp.com/ee-en/document/c07073462#AbT0)|64-bit Windows |OBS 29.0.2 |MJPEG, use WiFi IP, Enable audio, Allow hardware acceleration, deactivate when not showing |[Samsung 12M Ultrawide AF Camera Module](https://www.samsungsem.com/global/product/module/camera-module.do)|1920x1080 |MJPEG |TCP |[droidcam-obs-git](https://github.com/dev47apps/droidcam-obs-plugin) |[obs-studio-git](https://github.com/obsproject/obs-studio) |smooth, fast, clear |
|17. 03. 2023|raspivid |raspivid -fps 30 -t 0 -l -w 1920 -h 1080 -o tcp://0.0.0.0:3333 |[TL-WR802N 300Mbps N Nano Router](https://www.tp-link.com/us/home-networking/wifi-router/tl-wr802n/#specifications)|2.4GHz |460 |[Raspberry Pi Zero W](https://www.raspberrypi.com/products/raspberry-pi-zero-w/) |Raspberry Pi OS (32-bit) Lite|[Samsung Galaxy Note10](https://www.gsmarena.com/samsung_galaxy_note10-9788.php) |Android 12 |mpv-android 2023-02-27-release |mpv --cache=no --no-correct-pts --fps=30 --profile=low-latency tcp://<source device LAN IP>:3333 |Sony IMX219 |1920x1080 |MKV |TCP |[raspivid-git](https://github.com/raspberrypi/userland/blob/master/host_applications/linux/apps/raspicam/RaspiVid.c)|[mpv-android-git](https://github.com/mpv-android/mpv-android) |felt sluggish, slow [pi-camera#hardware-specification](https://www.raspberrypi.com/documentation/accessories/camera.html#hardware-specification) |
|17. 03. 2023|raspivid + FFmpeg|raspivid -fps 30 -t 0 -l -w 1920 -h 1080 -o udp://0.0.0.0:3333 |[TL-WR802N 300Mbps N Nano Router](https://www.tp-link.com/us/home-networking/wifi-router/tl-wr802n/#specifications)|2.4GHz |330 |[Raspberry Pi Zero W](https://www.raspberrypi.com/products/raspberry-pi-zero-w/) |Raspberry Pi OS (32-bit) Lite|[Samsung Galaxy Note10](https://www.gsmarena.com/samsung_galaxy_note10-9788.php) |Android 12 |mpv-android 2023-02-27-release |mpv --cache=no --no-correct-pts --fps=30 --profile=low-latency udp://<source device LAN IP>:3333 |Sony IMX219 |1920x1080 |MKV |UDP |[raspivid-git](https://github.com/raspberrypi/userland/blob/master/host_applications/linux/apps/raspicam/RaspiVid.c)|[mpv-android-git](https://github.com/mpv-android/mpv-android) |jittery, slow  [pi-camera#hardware-specification](https://www.raspberrypi.com/documentation/accessories/camera.html#hardware-specification) |
|05. 04. 2023|raspivid + FFmpeg|raspivid -vf -hf -fps 30 -t 0 -l -w 1920 -h 1080 --codec MJPEG -o - &#124;  ffmpeg -i - -vcodec copy -flush_packets 0 -listen 1 -f matroska udp://0.0.0.0:3333|[GL-SF1200 Dual-band gigabit Router](https://www.gl-inet.com/products/gl-sf1200/) |2.4GHz |260 |[Raspberry Pi Zero W](https://www.raspberrypi.com/products/raspberry-pi-zero-w/) |Raspberry Pi OS (32-bit) Lite|[OMEN Laptop 15-en1013dx Product Specifications](https://support.hp.com/ee-en/document/c07073462#AbT0)|64-bit Windows |mpv-x86_64-v3-20230514 |mpv --demuxer-thread=no --vd-lavc-threads=1 --untimed --no-correct-pts "udp://192.168.199.228:3333" |Sony IMX219 |1920x1080 |MP4 |UDP |[raspivid-git](https://github.com/raspberrypi/userland/blob/master/host_applications/linux/apps/raspicam/RaspiVid.c)|[mpv-player-git](https://github.com/mpv-player/mpv) |responsive, lossy when shaken |
|05. 04. 2023|raspivid |raspivid -vf -hf -fps 30 -t 0 -l -w 1920 -h 1080 --codec MJPEG -o - &#124;  ffmpeg -i - -vcodec copy -flush_packets 0 -listen 1 -f matroska tcp://0.0.0.0:3333|[GL-SF1200 Dual-band gigabit Router](https://www.gl-inet.com/products/gl-sf1200/) |2.4GHz |210 |[Raspberry Pi Zero W](https://www.raspberrypi.com/products/raspberry-pi-zero-w/) |Raspberry Pi OS (32-bit) Lite|[OMEN Laptop 15-en1013dx Product Specifications](https://support.hp.com/ee-en/document/c07073462#AbT0)|64-bit Windows |mpv-x86_64-v3-20230514 |mpv --demuxer-thread=no --vd-lavc-threads=1 --untimed --no-correct-pts "tcp://192.168.199.228:3333" |Sony IMX219 |1920x1080 |MP4 |TCP |[raspivid-git](https://github.com/raspberrypi/userland/blob/master/host_applications/linux/apps/raspicam/RaspiVid.c)|[mpv-player-git](https://github.com/mpv-player/mpv) |fast, smooth, sometimes stutters |
|28. 04. 2023|picamera2 |1080p, 30fps, medium JPEG quality (18Mbps) |[Samsung Galaxy Note10](https://www.gsmarena.com/samsung_galaxy_note10-9788.php) |2.4GHz |320 |[Raspberry Pi Zero W](https://www.raspberrypi.com/products/raspberry-pi-zero-w/) |Raspberry Pi OS (32-bit) Lite|[OMEN Laptop 15-en1013dx Product Specifications](https://support.hp.com/ee-en/document/c07073462#AbT0)|64-bit Windows |Brave Browser v1.52.64  (Chromium 112.0.5615.165)|N/A |Sony IMX219 |1920x1080 |MJPEG |HTTP |[picamera2/mjpeg_server.py](https://github.com/raspberrypi/picamera2/blob/main/examples/mjpeg_server.py) |[Brave-browser-git](https://github.com/brave/brave-browser) |responsive, fast, smooth, clear |
|28. 04. 2023|DroidCam OBS |tcp IP (set in OBS) |[Samsung Galaxy Note10](https://www.gsmarena.com/samsung_galaxy_note10-9788.php) |2.4GHz |256 |[Samsung Galaxy Note10](https://www.gsmarena.com/samsung_galaxy_note10-9788.php) |Android 12 |[OMEN Laptop 15-en1013dx Product Specifications](https://support.hp.com/ee-en/document/c07073462#AbT0)|64-bit Windows |OBS 29.0.2 |MJPEG, use WiFi IP, Enable audio, Allow hardware acceleration, deactivate when not showing |[Samsung 12M Ultrawide AF Camera Module](https://www.samsungsem.com/global/product/module/camera-module.do)|1920x1080 |MJPEG |TCP |[droidcam-obs-git](https://github.com/dev47apps/droidcam-obs-plugin) |[obs-studio-git](https://github.com/obsproject/obs-studio) |fast, smooth, crystal clear |
|29. 04. 2023|picamera2 |1080p, 30fps, Low JPEG quality (6Mbps) |[Samsung Galaxy Note10](https://www.gsmarena.com/samsung_galaxy_note10-9788.php) |2.4GHz |384 |[Raspberry Pi Zero W](https://www.raspberrypi.com/products/raspberry-pi-zero-w/) |Raspberry Pi OS (32-bit) Lite|[OMEN Laptop 15-en1013dx Product Specifications](https://support.hp.com/ee-en/document/c07073462#AbT0)|64-bit Windows |Godot_v4.0.2-stable_win64.exe |1080p |Sony IMX219 |1920x1080 |MJPEG |WebSocket|[stream_mjpeg_ws.py](https://github.com/mbz4/RoverXR/blob/main/Blueprints/stream_mjpeg_ws.py) |[Blueprints/Testing/websocket_2_py_demo](https://github.com/mbz4/RoverXR/tree/main/Blueprints/Testing/websocket_2_py_demo)|sluggish, clear |
|09. 05. 2023|picamera2 |720p, 30fps, Low JPEG quality (6Mbps) |[GL-SF1200 Dual-band gigabit Router](https://www.gl-inet.com/products/gl-sf1200/) |2.4GHz |256 |[Raspberry Pi Zero W](https://www.raspberrypi.com/products/raspberry-pi-zero-w/) |Raspberry Pi OS (32-bit) Lite|[OMEN Laptop 15-en1013dx Product Specifications](https://support.hp.com/ee-en/document/c07073462#AbT0)|64-bit Windows |Godot_v4.0.2-stable_win64.exe |720p | |1280x720 |MJPEG |WebSocket|[stream_mjpeg_ws.py](https://github.com/mbz4/RoverXR/blob/main/Blueprints/stream_mjpeg_ws.py) |[Blueprints/Testing/websocket_2_py_demo](https://github.com/mbz4/RoverXR/tree/main/Blueprints/Testing/websocket_2_py_demo)|responsive, little blurry |

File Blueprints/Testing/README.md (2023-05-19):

# Various tested raspivid, FFmpeg & MPV commands, arguments

### raspivid TCP H264
``` bash
raspivid -fps 30 -t 0 -l -w 1920 -h 1080 -o tcp://0.0.0.0:3333
```

### raspivid UDP H264
``` bash
raspivid -fps 30 -t 0 -l -w 1920 -h 1080 -o udp://0.0.0.0:3333
```

### raspivid MJPEG to FFmpeg MKV TCP
``` bash
raspivid -vf -hf -fps 30 -t 0 -l -w 1920 -h 1080 --codec MJPEG -o - | ffmpeg -i - -vcodec copy -flush_packets 0 -listen 1 -f matroska tcp://0.0.0.0:3333
```

### MPV low latency arguments TCP
``` bash
mpv --hwdec=auto --cache=no --no-correct-pts --fps=30 --profile=low-latency --opengl-glfinish=yes tcp://<RPi-IP>:3333
```

### MPV low latency arguments UDP
``` bash
mpv --hwdec=auto --cache=no --no-correct-pts --fps=30 --profile=low-latency --opengl-glfinish=yes udp://<RPi-IP>:3333
```

### MPV low latency arguments TCP (testing)
``` bash
mpv --demuxer-thread=no --vd-lavc-threads=1 --untimed --no-correct-pts "tcp://<RPi-IP>:3333
```

### raspivid MJPEG to custom py script (deprecated)
```bash
raspivid -vf -hf -fps 30 -t 0 -l -w 1920 -h 1080 --codec MJPEG -o - | python3 send_mjpeg.py
```

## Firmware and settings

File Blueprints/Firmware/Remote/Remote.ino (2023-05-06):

/*
    Description: JoyC will scan the mac address name of RoverC,
    press and hold the Home button of M5StickC on JoyC for 3 seconds to start
   scanning the hotspot of the car, and the pairing will be successful. After
   successful pairing, the link icon will be highlighted in the upper left
   corner of the screen, and the joystick value will be displayed on the screen.
   The left joystick controls the front and rear up and down, the left and right
   controls the pan, and the right joystick controls the left and right
   steering.
*/

#include <M5StickC.h>
#include <WiFi.h>
#include <WiFiUdp.h>
#include "EEPROM.h"

#define EEPROM_SIZE 64

TFT_eSprite Disbuff = TFT_eSprite(&M5.Lcd);
extern const unsigned char connect_on[800];
extern const unsigned char connect_off[800];

#define SYSNUM 3

uint64_t realTime[4], time_count = 0;
bool k_ready = false;
uint32_t key_count = 0;

IPAddress local_IP(192, 168, 4, 100 + SYSNUM);
IPAddress gateway(192, 168, 4, 1);
IPAddress subnet(255, 255, 0, 0);
IPAddress primaryDNS(8, 8, 8, 8);    // optional
IPAddress secondaryDNS(8, 8, 4, 4);  // optional

const char *ssid = "M5AP";
const char *password = "77777777";

WiFiUDP Udp;
uint32_t send_count = 0;
uint8_t system_state = 0;

void I2CWrite1Byte(uint8_t Addr, uint8_t Data) {
  Wire.beginTransmission(0x38);
  Wire.write(Addr);
  Wire.write(Data);
  Wire.endTransmission();
}

void I2CWritebuff(uint8_t Addr, uint8_t *Data, uint16_t Length) {
  Wire.beginTransmission(0x38);
  Wire.write(Addr);
  for (int i = 0; i < Length; i++) {
    Wire.write(Data[i]);
  }
  Wire.endTransmission();
}

uint8_t I2CRead8bit(uint8_t Addr) {
  Wire.beginTransmission(0x38);
  Wire.write(Addr);
  Wire.endTransmission();
  Wire.requestFrom(0x38, 1);
  return Wire.read();
}

uint16_t I2CRead16bit(uint8_t Addr) {
  uint16_t ReData = 0;
  Wire.beginTransmission(0x38);
  Wire.write(Addr);
  Wire.endTransmission();
  Wire.requestFrom(0x38, 2);
  for (int i = 0; i < 2; i++) {
    ReData <<= 8;
    ReData |= Wire.read();
  }
  return ReData;
}

bool joys_l = false;
uint8_t color[3] = { 0, 100, 0 };

uint8_t SendBuff[8] = { 0xAA, 0x55, SYSNUM, 0x00, 0x00, 0x00, 0x00, 0xee };

void SendUDP() {
  if (WiFi.status() == WL_CONNECTED) {
    Udp.beginPacket(IPAddress(192, 168, 4, 1), 1000 + SYSNUM);
    Udp.write(SendBuff, 8);
    Udp.endPacket();
  }
}

char APName[20];
String WfifAPBuff[16];
uint32_t count_bn_a = 0, choose = 0;
String ssidname;
void setup() {
  // put your setup code here, to run once:
  M5.begin();
  Wire.begin(0, 26, 100000UL);
  EEPROM.begin(EEPROM_SIZE);

  M5.Lcd.setRotation(4);
  M5.Lcd.setSwapBytes(false);
  Disbuff.createSprite(80, 160);
  Disbuff.setSwapBytes(true);

  Disbuff.fillRect(0, 0, 80, 20, Disbuff.color565(50, 50, 50));
  Disbuff.setTextSize(2);
  Disbuff.setTextColor(GREEN);
  Disbuff.setCursor(55, 6);
  // Disbuff.printf("%03d",SYSNUM);

  Disbuff.pushImage(0, 0, 20, 20, (uint16_t *)connect_off);
  Disbuff.pushSprite(0, 0);

  uint8_t res = I2CRead8bit(0x32);
  Serial.printf("Res0 = %02X \r\n", res);
  /*
    if( res & 0x02 )
    {
        I2CWrite1Byte(0x10,0x02);
    }
    else
    {
        Disbuff.setTextSize(1);
        Disbuff.setTextColor(GREEN);
        Disbuff.fillRect(0,0,80,20,Disbuff.color565(50,50,50));
        Disbuff.setCursor(5,20);
        Disbuff.printf("calibration");
        Disbuff.pushSprite(0,0);
        I2CWrite1Byte( 0x32 , 0x01 );
    }
    */
  M5.update();
  if ((EEPROM.read(0) != 0x56) || (M5.BtnA.read() == 1)) {
    WiFi.mode(WIFI_STA);
    int n = WiFi.scanNetworks();
    Disbuff.setTextSize(1);
    Disbuff.setTextColor(GREEN);
    Disbuff.fillRect(0, 0, 80, 20, Disbuff.color565(50, 50, 50));

    if (n == 0) {
      Disbuff.setCursor(5, 20);
      Disbuff.printf("no networks");

    } else {
      int count = 0;
      for (int i = 0; i < n; ++i) {
        if (WiFi.SSID(i).indexOf("M5AP") != -1) {
          if (count == 0) {
            Disbuff.setTextColor(GREEN);
          } else {
            Disbuff.setTextColor(WHITE);
          }
          Disbuff.setCursor(5, 25 + count * 10);
          String str = WiFi.SSID(i);
          Disbuff.printf(str.c_str());
          WfifAPBuff[count] = WiFi.SSID(i);
          count++;
        }
      }
      Disbuff.pushSprite(0, 0);
      while (1) {
        if (M5.BtnA.read() == 1) {
          if (count_bn_a >= 200) {
            count_bn_a = 201;
            EEPROM.writeUChar(0, 0x56);
            EEPROM.writeString(1, WfifAPBuff[choose]);
            ssidname = WfifAPBuff[choose];
            break;
          }
          count_bn_a++;
          Serial.printf("count_bn_a %d \n", count_bn_a);
        } else if ((M5.BtnA.isReleased()) && (count_bn_a != 0)) {
          Serial.printf("count_bn_a %d", count_bn_a);
          if (count_bn_a > 200) {
          } else {
            choose++;
            if (choose >= count) {
              choose = 0;
            }
            Disbuff.fillRect(0, 0, 80, 20, Disbuff.color565(50, 50, 50));
            for (int i = 0; i < count; i++) {
              Disbuff.setCursor(5, 25 + i * 10);
              if (choose == i) {
                Disbuff.setTextColor(GREEN);
              } else {
                Disbuff.setTextColor(WHITE);
              }
              Disbuff.printf(WfifAPBuff[i].c_str());
            }
            Disbuff.pushSprite(0, 0);
          }
          count_bn_a = 0;
        }
        delay(10);
        M5.update();
      }
      // EEPROM.writeString(1,WfifAPBuff[0]);
    }
  } else if (EEPROM.read(0) == 0x56) {
    ssidname = EEPROM.readString(1);
    EEPROM.readString(1, APName, 16);
  }

  Disbuff.fillRect(0, 20, 80, 140, BLACK);

  if (!WiFi.config(local_IP, gateway, subnet, primaryDNS, secondaryDNS)) {
    Serial.println("STA Failed to configure");
  }

  WiFi.begin(ssidname.c_str(), password);

  while (WiFi.status() != WL_CONNECTED) {
    delay(500);
    Serial.print(".");
  }

  Udp.begin(2000);

  Disbuff.pushImage(0, 0, 20, 20, (uint16_t *)connect_on);
  Disbuff.pushSprite(0, 0);
}

uint8_t adc_value[5] = { 0 };
uint16_t AngleBuff[4];
uint32_t count = 0;

void loop() {
  for (int i = 0; i < 5; i++) {
    adc_value[i] = I2CRead8bit(0x60 + i);
  }
  for (int i = 0; i < 4; i++) {
    AngleBuff[i] = I2CRead16bit(0x50 + i * 2);
  }
  delay(10);
  if (WiFi.status() != WL_CONNECTED) {
    Disbuff.pushImage(0, 0, 20, 20, (uint16_t *)connect_off);
    Disbuff.pushSprite(0, 0);
    count++;
    if (count > 500) {
      WiFi.config(local_IP, gateway, subnet, primaryDNS, secondaryDNS);
      count = 0;
    }
  } else {
    SendBuff[2] = adc_value[4];
    SendBuff[3] = map(AngleBuff[0], 0, 4000, 0, 200);
    SendBuff[4] = map(AngleBuff[1], 0, 4000, 0, 200);
    SendBuff[5] = map(AngleBuff[2], 0, 4000, 0, 200);
    if ((SendBuff[3] > 110) || (SendBuff[3] < 90) || (SendBuff[4] > 110) || (SendBuff[4] < 90) || (SendBuff[5] > 110) || (SendBuff[5] < 90)) {
      SendBuff[6] = 0x01;
    } else {
      SendBuff[6] = 0x00;
    }
    Serial.print(SendBuff[0], HEX); Serial.print("\t"); Serial.print(SendBuff[1], HEX); Serial.print("\t"); Serial.print(SendBuff[2], HEX); Serial.print("\t");
    Serial.print(SendBuff[3], HEX); Serial.print("\t"); Serial.print(SendBuff[4], HEX); Serial.print("\t"); Serial.print(SendBuff[5], HEX); Serial.print("\t");
    Serial.print(SendBuff[6], HEX); Serial.print("\t"); Serial.println(SendBuff[7], HEX);
    SendUDP();
  }
  
  Disbuff.fillRect(0, 30, 80, 130, BLACK);
  Disbuff.setCursor(10, 30);
  Disbuff.printf("%04d", SendBuff[3]);
  Disbuff.setCursor(10, 45);
  Disbuff.printf("%04d", SendBuff[4]);
  Disbuff.setCursor(10, 60);
  Disbuff.printf("%04d", SendBuff[5]);

  Disbuff.setCursor(10, 100);
  Disbuff.printf("%04d", adc_value[4]);
  // Disbuff.printf("%04X", adc_value[4]);
  Disbuff.setCursor(10, 115);
  Disbuff.printf("%04d", SendBuff[2]);
  Disbuff.pushSprite(0, 0);
}

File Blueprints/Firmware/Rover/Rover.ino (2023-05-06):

/*
    Description: RoverC will display "M5AP+2-byte mac address" hotspot name
   after booting up, waiting for JoyC to pair.
*/

#include <M5StickC.h>
#include <WiFi.h>
#include <WiFiUdp.h>
// #include "M5_RoverC.h"

const char *ssid = "M5AP";
const char *password = "77777777";

TFT_eSprite Disbuff = TFT_eSprite(&M5.Lcd);
WiFiServer server(80);

WiFiUDP Udp1;
// M5_RoverC roverc;

void SetChargingCurrent(uint8_t CurrentLevel) {
  Wire1.beginTransmission(0x34);
  Wire1.write(0x33);
  Wire1.write(0xC0 | (CurrentLevel & 0x0f));
  Wire1.endTransmission();
}

void setup() {
  M5.begin();
  M5.update();
  // roverc.begin();
  Wire.begin(0, 26, 100000UL);

  uint64_t chipid = ESP.getEfuseMac();
  String str = ssid + String((uint32_t)(chipid >> 32), HEX);
  M5.Lcd.setRotation(1);
  M5.Lcd.setSwapBytes(false);
  Disbuff.createSprite(160, 80);
  Disbuff.setSwapBytes(true);
  Disbuff.fillRect(0, 0, 160, 20, Disbuff.color565(50, 50, 50));
  Disbuff.setTextSize(2);
  Disbuff.setTextColor(WHITE);
  Disbuff.setCursor(15, 35);
  Disbuff.print(str);
  Disbuff.pushSprite(0, 0);

  SetChargingCurrent(4);

  Serial.begin(115200);
  // Set device in STA mode to begin with
  WiFi.softAPConfig(IPAddress(192, 168, 4, 1), IPAddress(192, 168, 4, 1),
                    IPAddress(255, 255, 255, 0));

  WiFi.softAP(str.c_str(), password);
  IPAddress myIP = WiFi.softAPIP();
  Serial.print("AP IP address: ");
  Serial.println(myIP);
  server.begin();

  Udp1.begin(1003);
}

uint8_t SendBuff[9] = { 0xAA, 0x55, 0x00, 0x00, 0x00, 0x00, 0x00, 0x00, 0xee };

uint8_t I2CWrite1Byte(uint8_t Addr, uint8_t Data) {
  Wire.beginTransmission(0x38);
  Wire.write(Addr);
  Wire.write(Data);
  return Wire.endTransmission();
}

uint8_t I2CWritebuff(uint8_t Addr, uint8_t *Data, uint16_t Length) {
  Wire.beginTransmission(0x38);
  Wire.write(Addr);
  for (int i = 0; i < Length; i++) {
    Wire.write(Data[i]);
  }
  return Wire.endTransmission();
}

int16_t speed_buff[4] = { 0 };
int8_t speed_sendbuff[4] = { 0 };
uint32_t count = 0;
uint8_t IIC_ReState = ESP_ERR_NO_MEM;

uint8_t Setspeed(int16_t Vtx, int16_t Vty, int16_t Wt) {
  Wt = (Wt > 100) ? 100 : Wt;
  Wt = (Wt < -100) ? -100 : Wt;

  Vtx = (Vtx > 100) ? 100 : Vtx;
  Vtx = (Vtx < -100) ? -100 : Vtx;
  Vty = (Vty > 100) ? 100 : Vty;
  Vty = (Vty < -100) ? -100 : Vty;

  Vtx = (Wt != 0) ? Vtx * (100 - abs(Wt)) / 100 : Vtx;
  Vty = (Wt != 0) ? Vty * (100 - abs(Wt)) / 100 : Vty;

  speed_buff[0] = Vty - Vtx - Wt;
  speed_buff[1] = Vty + Vtx + Wt;
  speed_buff[3] = Vty - Vtx + Wt;
  speed_buff[2] = Vty + Vtx - Wt;

  for (int i = 0; i < 4; i++) {
    speed_buff[i] = (speed_buff[i] > 100) ? 100 : speed_buff[i];
    speed_buff[i] = (speed_buff[i] < -100) ? -100 : speed_buff[i];
    speed_sendbuff[i] = speed_buff[i];
  }
  // Serial.println("Set speed...");
  return I2CWritebuff(0x00, (uint8_t *)speed_sendbuff, 4);
}

void setServoAngle(uint8_t pos, uint8_t angle) {
    uint8_t reg = 0x10 + pos;
    I2CWritebuff(reg, &angle, 1);
}

void loop() {
  int udplength = Udp1.parsePacket();
  if (udplength) {
    char udpdata[udplength];
    Udp1.read(udpdata, udplength);
    IPAddress udp_client = Udp1.remoteIP();
    if ((udpdata[0] == 0xAA) && (udpdata[1] == 0x55) && (udpdata[7] == 0xee)) {
      for (int i = 0; i < 8; i++) {
        Serial.printf("%02X ", udpdata[i]);
      }
      Serial.println();
      if (udpdata[6] == 0x01) {
        IIC_ReState = Setspeed(udpdata[3] - 100, udpdata[4] - 100,
                               udpdata[5] - 100);
      } else {
        IIC_ReState = Setspeed(0, 0, 0);
      }
      if (udpdata[2] != 0x00) {
        switch (udpdata[2]) {
          case 0x01:
            setServoAngle(0, 75); // Serial.println("RIGHT Trigger Pressed");
            break;
          case 0x10:
            setServoAngle(0, 20); // Serial.println("LEFT Trigger Pressed");
            break;
          case 0x11:
            setServoAngle(0, 2); // Serial.println("BOTH Triggers Pressed");
            break;
        }
      }
    } else {
      IIC_ReState = Setspeed(0, 0, 0);
    }
  }
  count++;
  if (count > 100) {
    count = 0;

    Disbuff.fillRect(0, 0, 160, 20, Disbuff.color565(50, 50, 50));
    Disbuff.setTextSize(1);
    Disbuff.setTextColor(WHITE);
    Disbuff.setCursor(5, 5);
    Disbuff.printf("%.2fV,%.2fmA,%d", M5.Axp.GetBatVoltage(),
                   M5.Axp.GetBatCurrent(), IIC_ReState);
    Disbuff.pushSprite(0, 0);
  }
}

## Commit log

2023-04-25 debugging tcp
    [rover_mod_kit.3mf]
2023-04-25 working servo on rover
2023-04-26 added gdscript files for godot project
    [export_presets.cfg]
2023-04-28 head of sockets ache very
2023-04-29 test framerate, autofocus controls w/ libcamera
2023-04-29 will this fix the buffer error?
    [stream_mjpeg_ws.py]
2023-04-30 need advice how to handle keyboard interrupt
2023-04-30 added v2 modkit CAD
    [adjustable_camera_shroud_mount_w_lens.3mf, adjustable_camera_shroud_mount_w_lens.step, camera_mounting_shroud v15.3mf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]
2023-05-01 add Pi2AR
    [export_presets.cfg]
2023-05-01 removed gd msc project
    [export_presets.cfg]
2023-05-02 added test lens mount + new animation w/ screws
    [camera_mounting_shroud v15.3mf, camera_mounting_shroud_3,04mm_focal_adjust v10.3mf]
2023-05-02 more cad files, update readme w/ BOM...
    [assorted_camera_mounts.3mf, camera_mounting_shroud v16.3mf, camera_mounting_shroud_3,04mm_focal_adjust v11.3mf]
2023-05-02 added 3mf of lens mount, improved
    [camera_mounting_shroud v21.3mf]
2023-05-03 rear bumper changes, install script add pwd, readme
    [rear_port_bumber v32.3mf]
2023-05-03 added screenshots with various lenses
2023-05-04 added maglock adapter kit, cleaned repo
    [assorted_camera_mounts.3mf, bumper_maglock_adapter v23.3mf, bumper_maglock_adapter_cap v23.3mf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]
2023-05-08 adjusted screen, tuned camera focus for fisheye
2023-05-20 cleaning up git
    [export_presets.cfg]
